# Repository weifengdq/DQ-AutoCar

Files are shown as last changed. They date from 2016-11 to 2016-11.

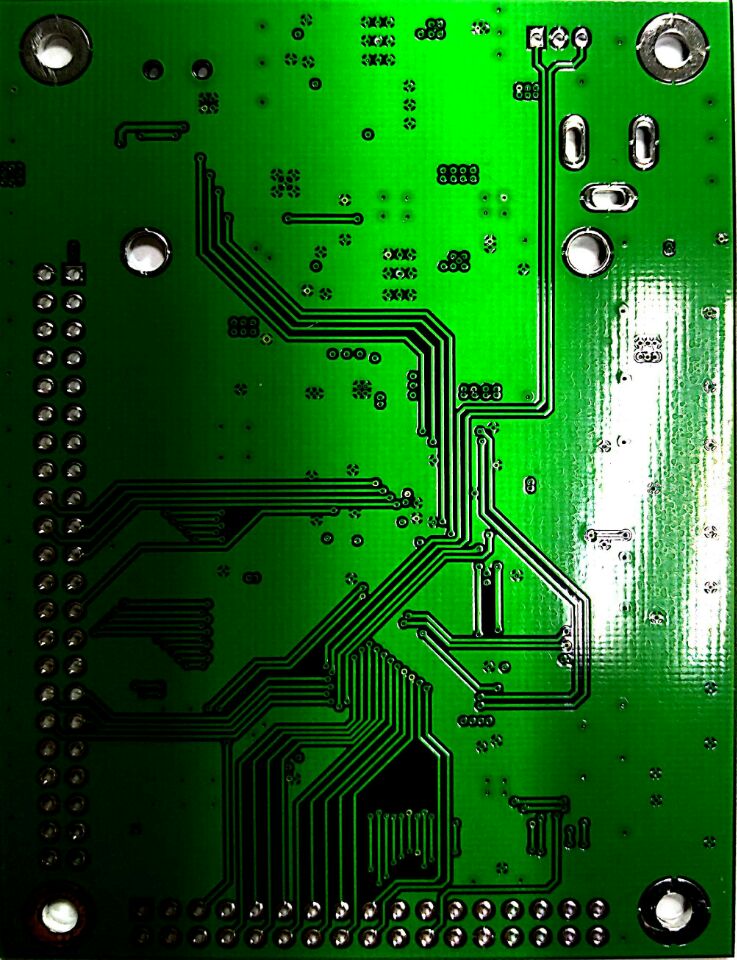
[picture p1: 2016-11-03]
PCB Image/AutoCar2.jpg

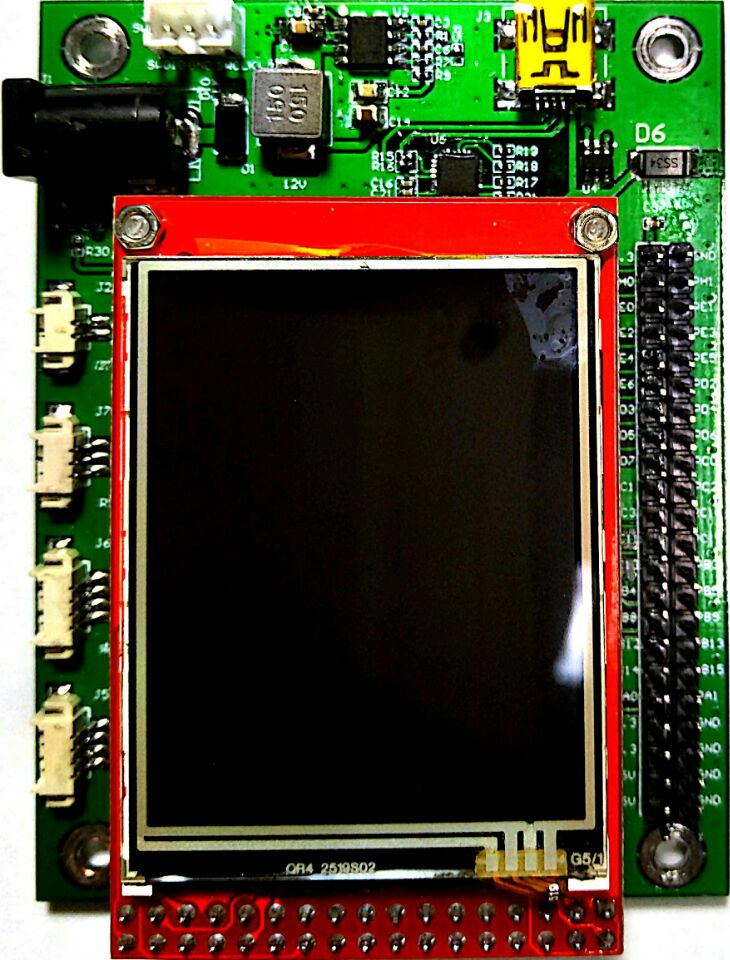
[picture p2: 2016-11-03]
PCB Image/AutoCar4.jpg

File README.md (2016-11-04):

# DQ-AutoCar
Test Programs and PCB for AutoCar

距离我第一次画PCB已经过去了5年, 期间断断续续, 这是首次尝试画4层PCB, 尽管它是非必须的. 但我还是迈出了这一步.   

Alitum Designer菜单栏中Design->Layer Stack Manager, 这样就可以添加层了, 四层板从上到下的顺序分别是: Top Layer, GND Plane, POWER Plane, Bottom Layer. 顶层和底层是Layer, 正片, 走线的地方是有铜的; 中间两层是Plane, 负片, 也就是走线的地方是没有铜的, 不走线的地方会默认敷铜. 一般GND Plane层是一整片的GND, POWER层可以按需要分割成12V, 5V, 3.3V等.    

板子资源:  
- 电源链路: 24V -> MP2303 -> 12V给雷达供电; 24V -> MP2303 -> 5V -> 3.3V;  
- MCU: STM32F207VCT6;  
- 通信: CP2105(USB转双串口), MAX3232(RS232), 共3路串口;  
- 显示: 2.2寸320x240 LCD, 使用FSMC刷屏;  
- MH1.25-4P接口: 编码器接口, 前后向开关接口;  

功能比较简单, 但为了好看些, 画出来这么大一板子(6.6cm * 8.8cm), 一个面都没有摆满...

板子用了一周才回来, 手动焊了3块, 用酒精棉擦了擦, 然后用热风枪吹化白色的残留松香, 这样看起来漂亮一些, 检查一下上电很顺利, 除了那个24V转12V的部分容易出问题, 大概是功率电感下面不能铺铜吧, 输出只有不到5V, 我把功率电感抬高才正常输出到11.88V.  

使用的话需要先安装CP2105的驱动, 会在设备管理器中出现两个串口.

现学现卖的使用 STM32CubeMX + HAL库 写了板子的几个测试程序, 才花了不到3个小时, 真的挺好使.  很推荐这种写法, 因为不论STM32那个型号, 你都不用关心时钟啊, 底层驱动啊之类的, 鼠标在STM32CubeMX中点一点就好了, 给你留出更多的时间去写功能性的东西.  

参考的话:
- Description of STM32F2xx HAL drivers.pdf
- STM32F205xx, STM32F207xx, STM32F215xx and STM32F217xx advanced ARM-based 32-bit MCUs_Reference manual.pdf
- STM32F207VET6_PDF_C59126_2015-10-07_Datasheet.pdf   

这3个文档都是需要看一下的.

另外, STM32同引脚数量不同型号的引脚是兼容的, 也就是说, 板子用到100个引脚的F103Vxx, F407Vxx之类的也是可以的.

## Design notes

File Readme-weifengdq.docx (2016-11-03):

## 开篇

STM32F207VCT6, 外部晶振12MHz.

参考微雪课堂的STM32CubeMX系列教程:

http://www.waveshare.net/study/portal.php?mod=list&catid=38

## PCB问题汇总

12M晶振引脚用错了, 应为PH0-OSC_IN, PH1-OSC_OUT, 图中接的是32.768kHz的引脚.

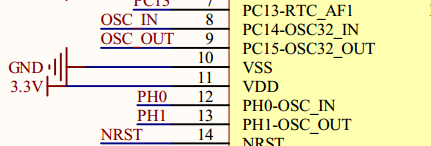
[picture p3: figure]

CP2105与USB的D+, D-接反了. 飞了3个7.5Ω的电阻.

TL431的电路参数有些问题, 而且封装引脚错了.

MP2303的输入输出都应该接100nF的电容, 而且功率电感下面不应该铺铜, 否则12V的电压可能输出不了. 抬高了功率电感, 建议下次铺铜前把功率电感下面圈住不铺铜.

M7用SS34代替了.

2P, 3P, 4P端子的接地焊盘应该像USB那样多铺铜, 仅十字接地很容易拽掉焊盘.

添加复位按键, 很有用.

## Blink

LED0--PA11, 标号D4, 高电平点亮.

LED1—PA12, 标号D5, 高电平点亮.

实现LED0, LED1每s变换一次状态. 参考:

http://www.waveshare.net/study/article-630-1.html

## EXIT

设置PA0(WAKEUP)上拉, 下降沿触发外部中断, 然后用杜邦线触碰PA0和GND. 中断函数中改变LED0的状态.

## Basic_TIM

基本定时器的应用, 用定时器3实现每1s翻转一下两个LED的状态.

60 000 000MHz, 设置分频置60000-1, 计数周期为10-1, 即10ms中断一次.

## PWM

使用PB8(TIM4_CH3), PB9(TIM4_CH4)输出10kHz PWM. 通道3, 4占空比分别为80%, 20%.

60 000 000MHz, 设置分配60-1, 计数周期100-1, Pulse是设置脉宽的, 这里先不设置, 手动写程序设置.

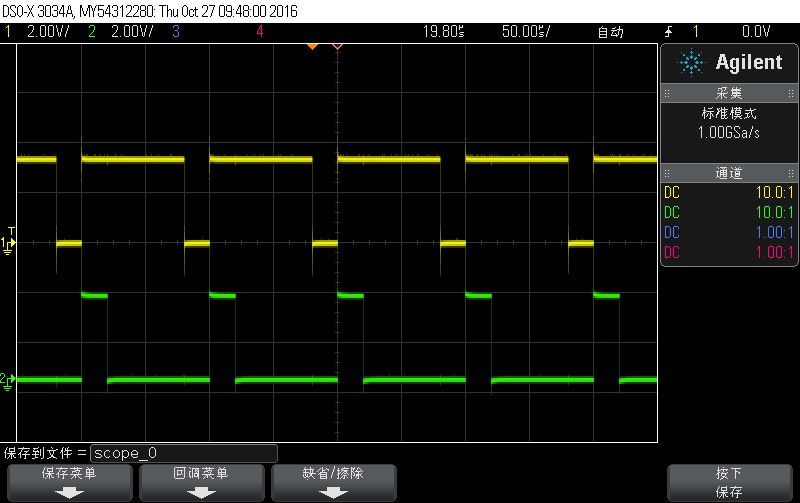
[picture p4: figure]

## UART_Printf

PA9----USART1_TX

PA10---USART1_RX

接到了MAX3232

PA2----USART2_TX

PA3----USART2_RX

接到了CP2105的小号串口

PB10---USART3_TX

PB11---USART3_RX

接到了CP2105的大号串口

printf重定向到USART1, 即连接到MAX3232的那个, 也就是只能USART1使用printf. 可否有printf2, printf3? 串口波特率均设置为115200Bits/s. 记得安装CP2105的驱动.

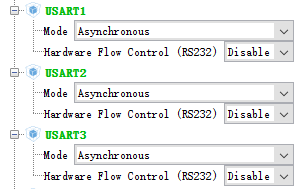
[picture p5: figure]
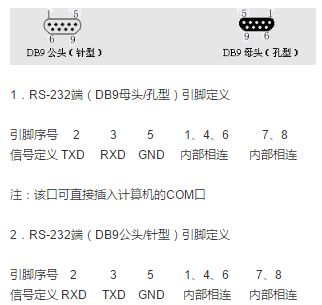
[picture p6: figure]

COM22是UART1, COM16是UART2, COM17是UART3.

板子RS232接口的R, GND, T引脚分别接DB9公头RS232的3(RXD), 5(GND), 2(TXD), 不用交叉.

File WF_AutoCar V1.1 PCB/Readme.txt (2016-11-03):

V1.1 升级日志:

12M晶振引脚用错了, 应为PH0-OSC_IN, PH1-OSC_OUT, V1.0接的是32.768kHz的引脚, V1.1已经修正.
 
CP2105与USB的D+, D-接反了. V1.0飞了3个7.5Ω的电阻, V1,1已修正.
 
TL431的电路参数有些问题, 而且封装引脚错了, V1,1已修正.

MP2303的输入输出都应该接100nF的电容, 而且功率电感下面似乎不应该铺铜, 否则12V的电压可能输出不了. 抬高了功率电感, V1.1已修正.

M7用SS34代替.

2P, 3P, 4P端子的接地焊盘多铺铜, 仅十字接地很容易拽掉焊盘, V1.1已修正.

添加复位按键, V1.1暂未修正.

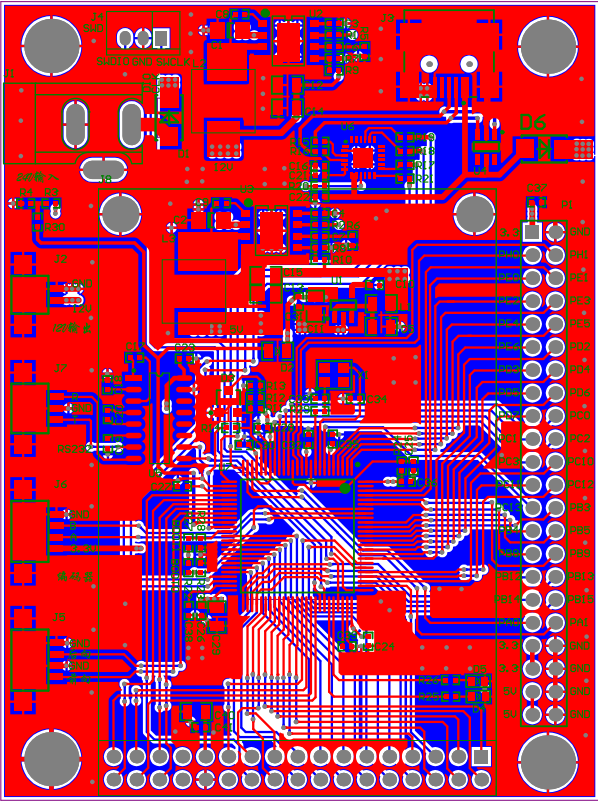
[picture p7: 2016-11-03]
PCB Image/AutoCar5.png

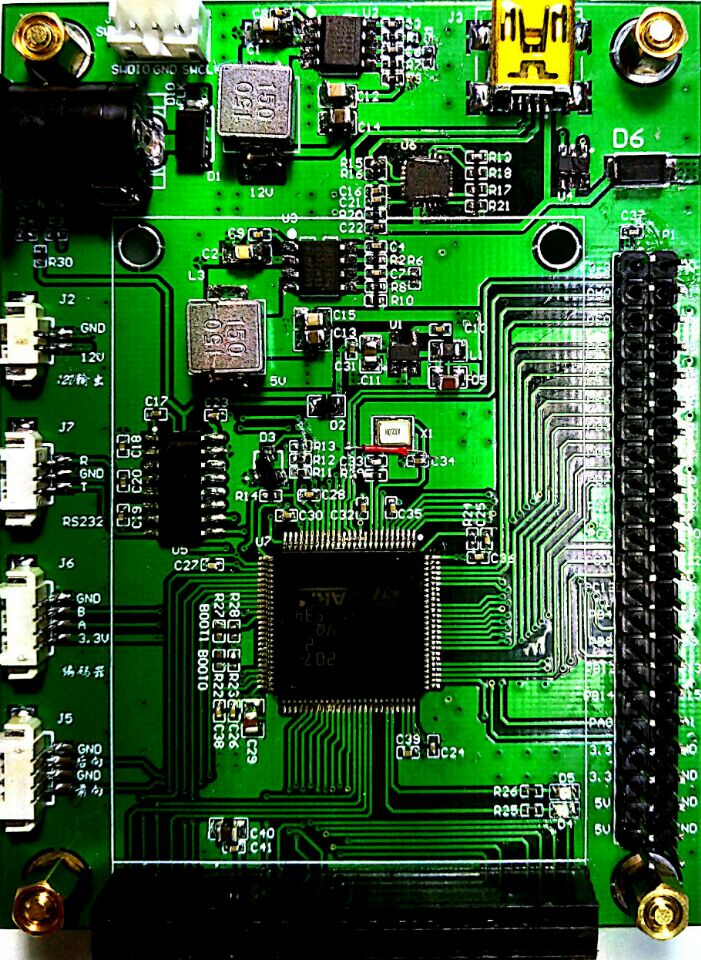
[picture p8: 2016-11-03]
PCB Image/AutoCar3.jpg

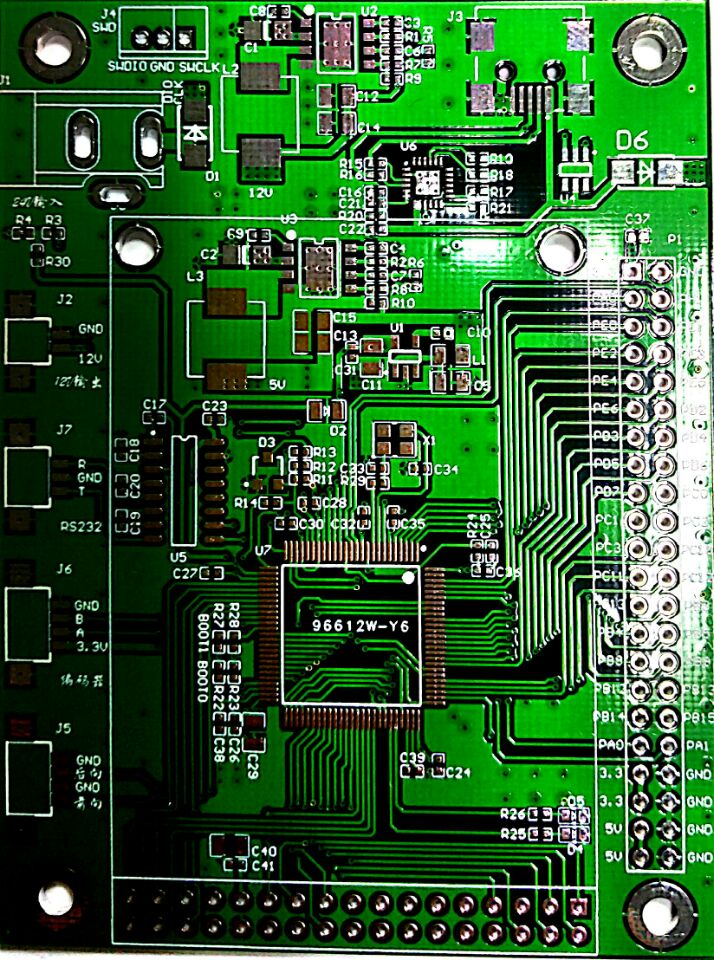
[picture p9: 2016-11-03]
PCB Image/AutoCar1.jpg

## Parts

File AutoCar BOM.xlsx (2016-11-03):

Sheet: BOM Report
Bill of Materials |  |  | <Parameter Title not found>
Source Data From: |  | WF_AutoCar.PrjPcb
Project: |  | WF_AutoCar.PrjPcb
Variant: |  | None
Creation Date: | 11/3/2016 | 11:09:48 AM
Print Date: | 42677 | 42677.48174
Footprint | Comment | LibRef | Designator | Description | Quantity | 参考价格(元/只) | 共计(元)
C1206 | Cap1 | Cap1 | C1, C2 | Capacitor | 2 | 0.05 | 0.1
C0402 | Cap1 | Cap1 | C3, C4, C6, C7, C8, C9, C10, C16, C17, C18, C19, C20, C21, C22, C23, C24, C25, C26, C27, C28, C30, C31, C32, C33, C34, C35, C36, C37, C38, C39, C41 | Capacitor | 31 | 0.01 | 0.31
CC0805 | Cap1 | Cap1 | C5, C11, C12, C13, C14, C15, C29, C40 | Capacitor | 8 | 0.01 | 0.08
LC-SMA(DO-214AC)_S2 | M7 | Diode1 | D1, D6 |  | 2 | 0.04 | 0.08
Diode-0805 | 1N4148 | Diode1 | D2 |  | 1 | 0.08 | 0.08
SOT-23 | TL431 | TL431-SOT23 | D3 |  | 1 | 0.09 | 0.09
DIODE-12 | LED0 | LED1 | D4 | Typical INFRARED GaAs LED | 1 | 0.08 | 0.08
DIODE-12 | LED1 | LED1 | D5 | Typical INFRARED GaAs LED | 1 | 0.08 | 0.08
DC10B | DC-005 | DC-005 | J1 |  | 1 | 0.18 | 0.18
MH1.25*2立式FR | MH1.25*2卧式FR | MH1.25*2卧式FR | J2 |  | 1 | 0.6 | 0.6
USB/SM0.8-6H5 | USB-PORT | USB-PORT | J3 | mini-USB | 1 | 0.1 | 0.1
Con3_2.0 | 2.0*3 | Con3_2.0 | J4 | Header, 3-Pin, XH2.0-3P | 1 | 0.12 | 0.12
MH1.25*4立式Pi | MH1.25*4卧式 前向开?D GaA | MH1.25*4立式 前 | J5 |  | 1 | 0.8 | 0.8
MH1.25*4立式 前 | MH1.25*4卧式 编?开?D | MH1.25*4立式 编 | J6 |  | 1 | 0.8 | 0.8
MH1.25*3立式 编 | MH1.25*3卧式贴片 R?D G | MH1.25*3卧式贴片 | J7 |  | 1 | 0.7 | 0.7
2.2TFT_ILI9325 | LCD2.2 | 2.2 LCD ILI9325 | J8 |  | 1 | 25 | 25
CC0805 | BLM18 | BLM18 | L1 |  | 1 | 0.2 | 0.2
0630 | Inductor | Inductor | L2, L3 | Inductor | 2 | 0.4 | 0.8
HDR2X22 | Header 22X2 | Header 22X2 | P1 | Header, 22-Pin, Dual row | 1 | 0.48 | 0.48
C0402 | Res1 | Res1 | R1, R2, R3, R4, R5, R6, R7, R8, R9, R10, R11, R12, R13, R14, R15, R16, R17, R18, R19, R20, R21, R22, R23, R24, R25, R26, R27, R28, R29, R30 | Resistor | 30 | 0.01 | 0.3
LC-SOT-23-5 | SP6205EM5-L-3-3 | SP6205EM5-L-3-3 | U1 |  | 1 | 0.6 | 0.6
LC-SOIC-8_150mil | MP2303 | MP2307 | U2, U3 |  | 2 | 1.3 | 2.6
LC-SOT-23-6 | SRV05-4.TCT | SRV05-4.TCT | U4 |  | 1 | 0.22 | 0.22
SOP16M | MAX3232 | MAX3232 | U5 |  | 1 | 0.35 | 0.35
QFN-24 | CP2105 | CP2105 | U6 |  | 1 | 11 | 11
LC-LQFP-100_14x14x05P | STM32F207VET6 | STM32F207VET6 | U7 |  | 1 | 19.5 | 19.5
XTAL-3225 | 12M | XTAL_1 | X1 | Crystal Oscillator | 1 | 0.38 | 0.38
 |  |  |  |  | 97 |  | 65.63
Approved |  | Notes
 |  |  |  |  |  | 元器件共计 65.63 元 PCB平均 25 元 总计 90.63 元

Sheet: Project Information
Project Full Path | C:\Users\weifengdq\Documents\NutCloud\我的坚果云\Job\Altium\WF_AutoCar\WF_AutoCar.P8, R1
Project Filename | WF_AutoCar.PrjPcb
Variant Name | None
Data-Source Filename | WF_AutoCar.PrjPcb
Data-Source Full Path | C:\Users\weifengdq\Documents\NutCloud\我的坚果云\Job\Altium\WF_AutoCar\WF_AutoCar.P8, R1
Title | <Parameter Title not found>
Total Quantity | 97
Report Time | 11:09:48 AM
Report Date | 11/3/2016
Report Date & Tine | 11/3/2016 11:09:48 AM
Output Name | Bill of Materials
Output Type | BOM_PartType
Output Generator Name | BOM
Output Generator Description | Bill of Materials

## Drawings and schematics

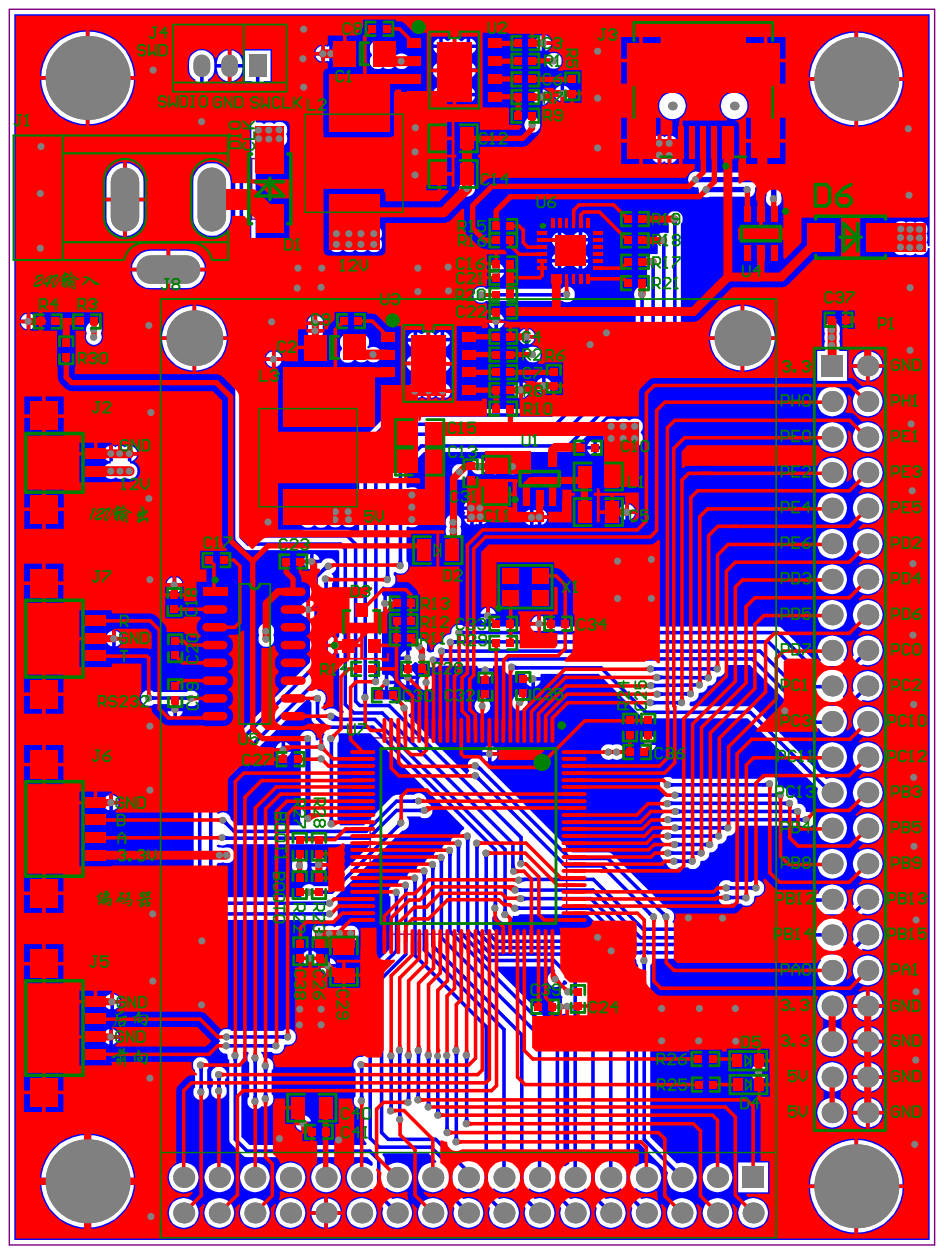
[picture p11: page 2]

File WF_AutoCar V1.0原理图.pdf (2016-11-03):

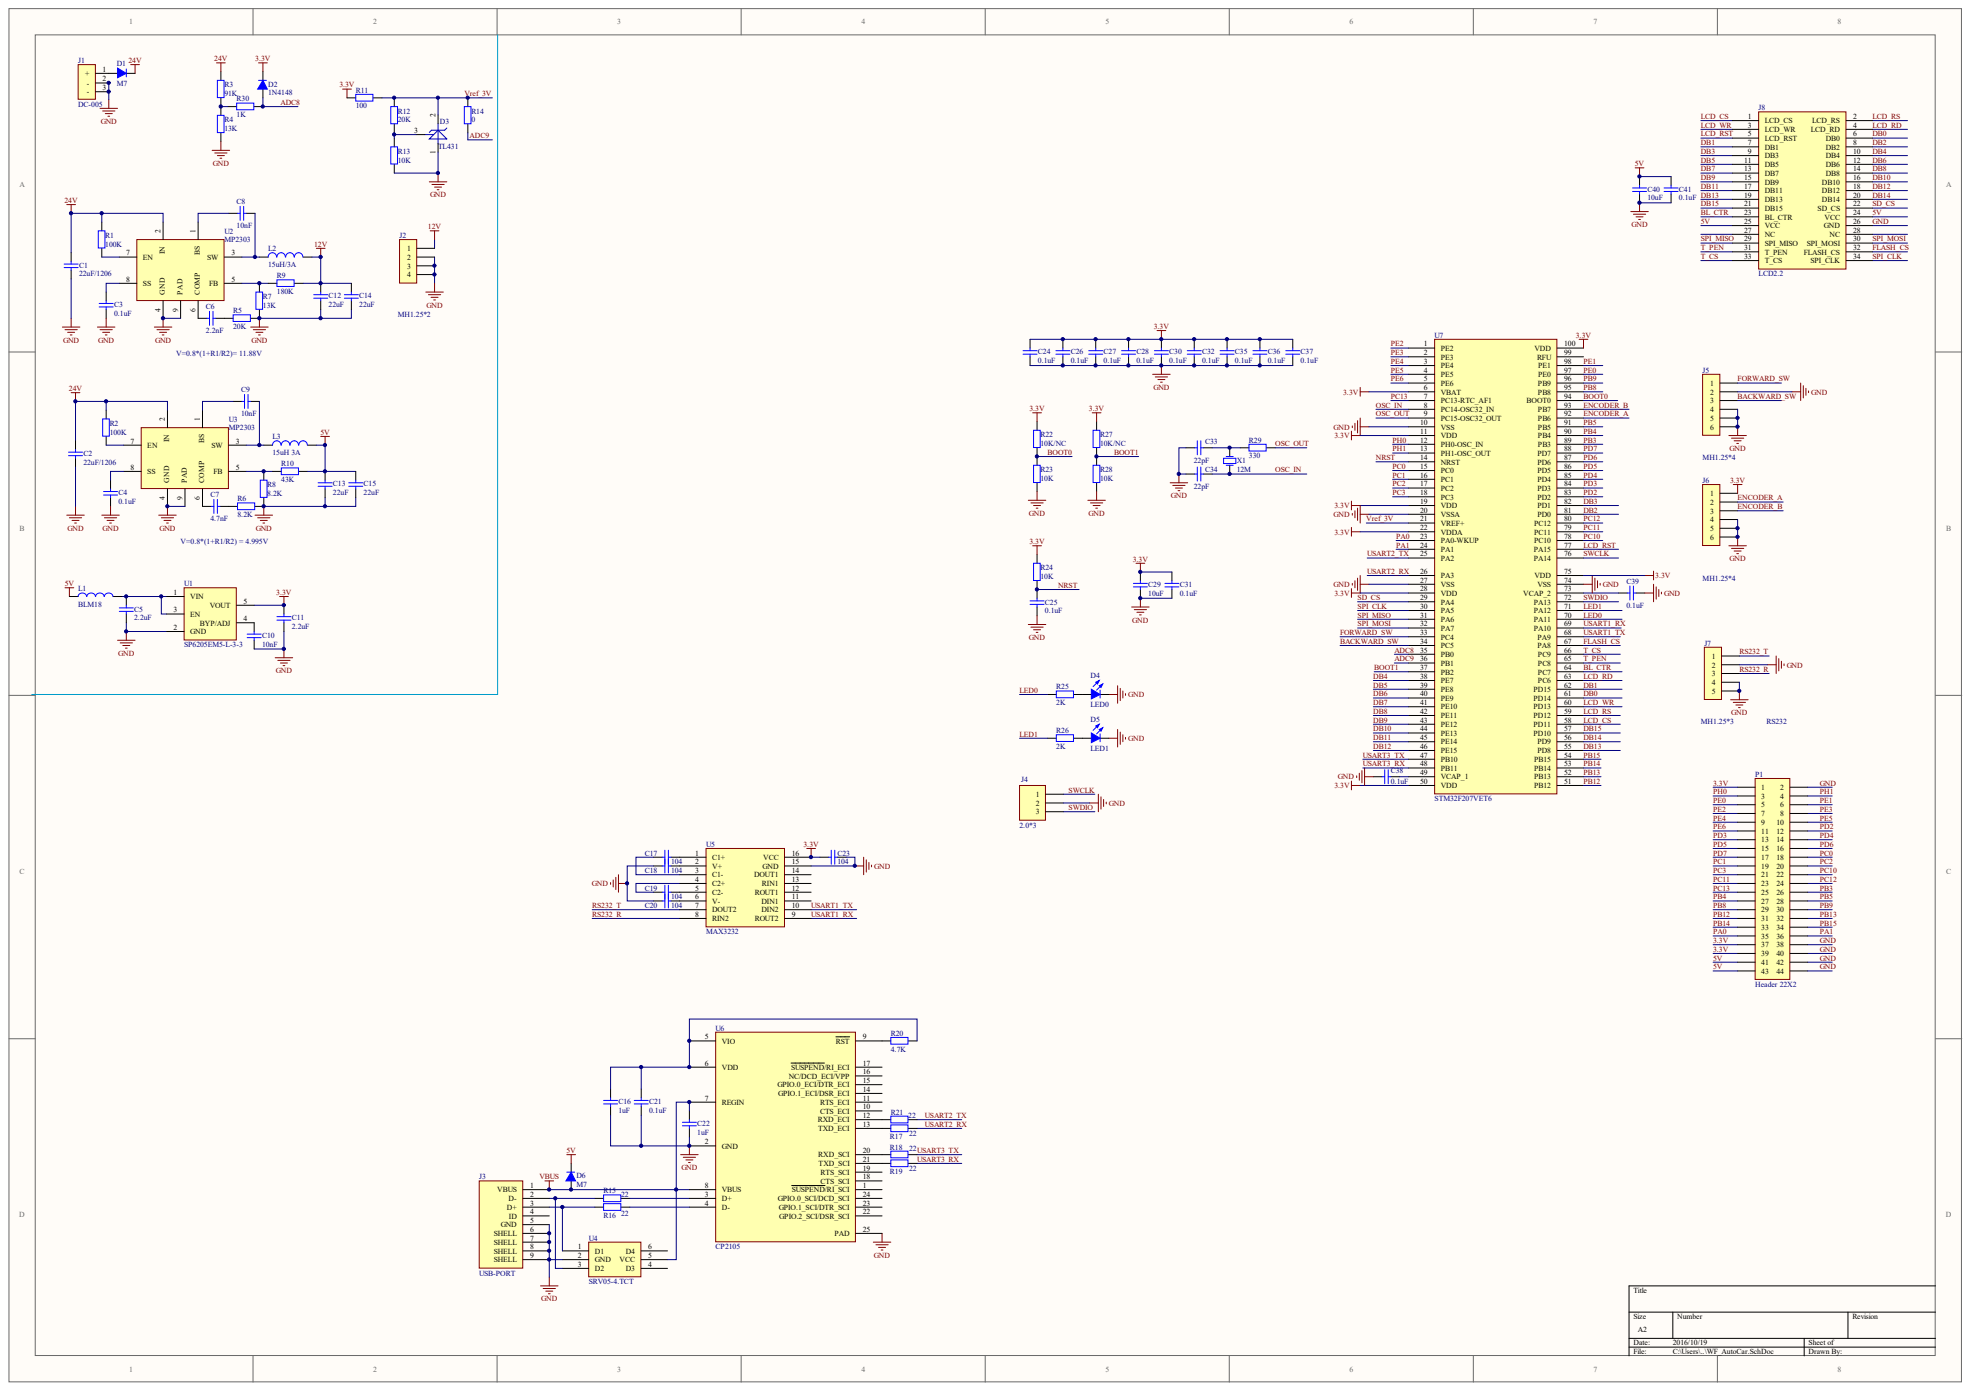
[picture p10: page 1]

2 2 2 | 3
